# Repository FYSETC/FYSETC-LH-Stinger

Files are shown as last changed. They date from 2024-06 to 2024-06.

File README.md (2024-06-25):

# FYSETC-LH-Stinger
FYSETC LH-Stinger 3D printer library

# Introduction

This is a project from lhndo community,LH-Stinger . We made a little upgrade and improvement on the basis of this project, and provided a complete set of information. Thanks to the open source materials and support provided by Andrei, and hope you like it. You can find LH-Stinger official information below.

1.LH-Stinger Official website：

https://github.com/lhndo/LH-Stinger

2.LH-Stinger FYSETC Kit Wiki：
https://github.com/lhndo/LH-Stinger/wiki/FYSETC-Kit#issues

# BOM

[ LH-Stinger](https://github.com/FYSETC/FYSETC-LH-Stinger/blob/main/BOM.md)

# STL changes

### FYSETC LH-Stinger STLs changes
The following parts are required to match the component configuration of the FYSETC kit:

Toolhead:
[Toolhead Dragon UHF + Sherpa Mini](https://github.com/lhndo/LH-Stinger/tree/main/User_Mods/Toolhead/Toolhead%20Dragon%20UHF%20%2B%20Sherpa%20%20Mini%20-%20%40LH)

Aux Fan:
[Flap UHF x2](https://github.com/lhndo/LH-Stinger/blob/main/STL/Printer/Aux%20Fan/Flap%20UHF%20x2.stl)
Included in [STL/Aux Fan Parts.3mf ](https://github.com/lhndo/LH-Stinger/tree/main/STL)(Plate: Optional UHF )

Ebox:
[FYSETC Spider Mount](https://github.com/lhndo/LH-Stinger/tree/main/User_Mods/Ebox/FYSETC%20Spider%20V3%20Mount%20-%20%40MakerMylo)
Panel Bottom for LM200-22B48R2 Power Supply Check it [here](https://github.com/FYSETC/FYSETC-LH-Stinger/tree/main/STLs/Panel%20Bottom%20for%20LM200-22B48R2%20Power%20Supply)

LHS Breakbeat - Breakout Box:
[Breakout Box](https://github.com/lhndo/LH-Stinger/tree/main/STL/Printer/Breakout%20Box)
Included in [STL/Breakout Box Parts.3mf](https://github.com/lhndo/LH-Stinger/tree/main/STL)

# Wiring

### FYSETC LH-Stinger kit wiring



# Installation Guide

LH-Stinger Assembly manual [here](https://github.com/lhndo/LH-Stinger/wiki/Assembly-Guide).

MakerMylo Assembly manual [here](https://help.mylo.fun/makermylo-documents/fysetc/lh-stinger/youtube-build-series).

# Firmware&OS

Check it [here](https://github.com/FYSETC/FYSETC-LH-Stinger/tree/main/Klipper_Config).

# Videos

### Original LH-Stinger Videos [here](https://www.youtube.com/channel/UCPD2Ai4b49gVoCFSGFWoSdw).

# Support

FYSETC Facebook group: 

https://www.facebook.com/groups/238970713918171

FYSETC Discord:

https://discord.gg/T3XcJPgr

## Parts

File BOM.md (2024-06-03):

# Package list 

## LH Stinger Revision 1.0

| Index | Sort | Component | Qty | Note |
| ----- | --- | --- | --- | --- |
| 1 | Fasteners | LH Stinger fasteners Pack（12.9） | 1 SET  | |
| 2 | Frame | X Gantry 2020 323mm | 1 PC | |
| 3 | Frame | Y 3090 345mm | 1 PC | |
| 4 | Frame | Z Pillars 3060 400mm | 2 PCS  | |
| 5 | Frame | Z Top 3030 400mm | 1 PC | |
| 6 | Frame | Z Bottom 3090 400mm | 1 PC | |
| 7 | Frame | Y Rubber Feet 28 x 22 x 16.5mm | 4 PCS  | |
| 8 | Frame | Z Frame Feet - Flat Rubber, Neoprene Stiff Foam - 5mm, 1/4"  | 2 PCS  | |
| 9 | Frame | T Bracket Plate (Bottom,Enlarging the hole) | 2 PCS  | |
| 10 | Frame | Three Way Corner | 2 PCS  | |
| 11 | Frame | Bracket 90 No Tabs | 4 PCS  | |
| 12 | Frame | Bracket 90 No Tabs (Enlarging the hole) | 2 PCS  | |
| 13 | Frame | Bracket 90 Cast Tabs | 4 PCS  | |
| 14 | Motion | MGN 12H 300mm (Z1+ preload) stainless steel  440C | 3 PCS  | |
| 15 | Motion | MGN 12H 250mm (Z1+ preload) stainless steel  440C | 2 PCS  | |
| 16 | Motion | GATES GT2 Belt Loop (6mm W) - 188mm | 2 PCS  | |
| 17 | Motion | GATES GT2 Open Belt LL-2GT-6 (6mm wide) - 3000mm | 1 PC | |
| 18 | Motion | GATES GT2 Open Belt LL-2GT-9 (9mm wide) - 1000mm | 1 PC | |
| 19 | Motion | Pulley Gates 2GT 6mm Runice | 5 PCS  | |
| 20 | Motion | Pulley Gates 2GT 9mm (max 20mm height) Runice | 2 PCS  | |
| 21 | Motion | Pulley Gates 2GT 80 Tooth 6mm Runice | 2 PCS  | |
| 22 | Motion | Idler Gates 2GT 6mm Tooth (15mm outer ring diameter) Runice  | 3 PCS  | |
| 23 | Motion | Idler Gates 2GT 9mm Tooth Runice | 2 PCS  | |
| 24 | Motion | Bearing 625 2RS FUSHI | 8 PCS  | |
| 25 | Motion | Shaft Round 5x25mm (Idlers) | 3 PCS  | |
| 26 | Motion | Shaft Round 5x30mm (Idlers) | 2PCS | |
| 27 | Motion | D shaft 50x5mm (Z stack) | 1 PC | |
| 28 | Motion | D shaft 72x5mm (Z stack) | 1 PC | |
| 29 | Buildplate  | LH Stinger 200 CF Bed set | 1 SET  | |
| 30 | Buildplate  | PEI Film (200 mm^2) | 1 PC | |
| 31 | Buildplate  | Hotbed Kit for 200x200 220W | 1 PC | |
| 32 | Buildplate  | PI tape (50mm Width ，30M length) | 1 PC | |
| 33 | Misc | Sherpa mini CNC Extruder | 1 SET  | |
| 34 | Misc | Dragon Hotend UHF | 1 SET  | |
| 35 | Misc | Heater Cartridge 24V 70W | 1 PC | |
| 36 | Misc | Thermistor PT1000 | 1 PC | |
| 37 | Controller  | Spider H723 Board | 1 SET  | |
| 38 | Electronics | Raspberrypi 4b 2GB | 1 SET  | Optional |
| 39 | Electronics | MicroSD Card 16 GB | 1 PC | |
| 40 | Electronics | USB A to USB C - 25cm | 1PC | |
| 41 | Electronics | TMC2209 Stepper Motor Driver | 3 PCS  | |
| 42 | Electronics | TMC5160 Stepper Motor Driver | 3 PCS  | |
| 43 | Electronics | Nozzle Input Shaper | 1 PC | |
| 44 | Electronics | NEMA17 Stepper motors 42HS3418-22B19  (check [here](https://github.com/FYSETC/FYSETC-LH-Stinger/tree/main/Stepper%20motor%20parameters) | 2 PCS  | |
| 45 | Electronics | NEMA17 Stepper motors 42HSC6406C-24B20  (check [here](https://github.com/FYSETC/FYSETC-LH-Stinger/tree/main/Stepper%20motor%20parameters)） | 3 PCS  | |
| 46 | Electronics | Power Supply  Meanwell LSR-350 | 1 PC | |
| 47 | Electronics | Power Supply MORNSUN LM200-22B48R2 (HV X, Y Steppers) | 1 PC | |
| 48 | Electronics | Raspberry Pi communication cable | 1 PC | |
| 49 | Electronics | Dual Ball FAN - 5015 24V (Part Fan) | 2 PCS  | |
| 50 | Electronics | Dual Ball FAN - 4010 24V(Hotend Fan) | 1 PC | |
| 51 | Electronics | Dual Ball FAN - 6025 24V (Ebox Fan) | 2 PCS  | |
| 52 | Electronics | Dual Ball FAN - 9733 24V (AUX Fan) | 2 PCS  | |
| 53 | Electronics | Microswitch OMRON D2F-5 (Quickdraw Probe) with wire | 1 PC | |
| 54 | Electronics | 3 PIN Omron Endstops with wire | 3 PCS  | |
| 55 | Electronics | AC 250V 3 Terminal Power Socket with Fuse | 1 SET  | |
| 56 | Electronics | AC Power Cord | 1 PC | |
| 57 | Misc | Wiring kit（Pre-crimped terminals and longer wire lengths with label） | 1 SET  | |
| 58 | Electronics | LHS Breakbeat Board | 1 SET  | |
| 59 | Misc | Weaving casing 5mm 2.5M | 1 PC | |
| 60 | Misc | Weaving casing 8mm 2.0M | 1 SPC  | |
| 61 | Misc | Tension spring | 8 PCS  | |
| 62 | Misc | 4mm Bowden Coupler | 2 PCS  | |
| 63 | Misc | PTFE Tube (4mm OD 2mm ID) - 0.1m | 1 PC | |
| 64 | Misc | PTFE Tube (4mm OD 3mm ID) - 0.6m | 1 PC | |
| 65 | Misc | 6x3 Round Magnet (Quickdraw and Y Belt Set Tool) | 12 PCS | |
| 66 | Misc | Cutting pliers | 1 PC | |
| 67 | Misc | Hexagonal wrenchs | 1 SET  | |
| 68 | Misc | Thermal silica | 1 PC | |
| 69 | Misc | Ties | 20 PCS | |

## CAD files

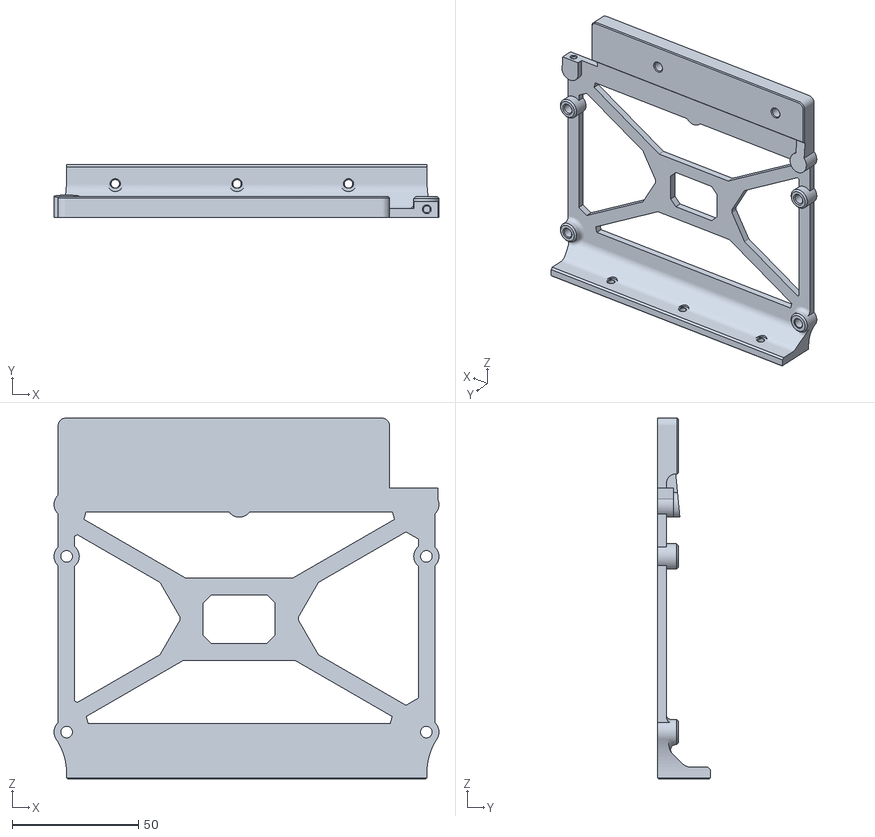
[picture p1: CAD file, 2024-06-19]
STLs/Mount Spider H7/Mount Spider H7.STL
152.3 x 20.8 x 142.7

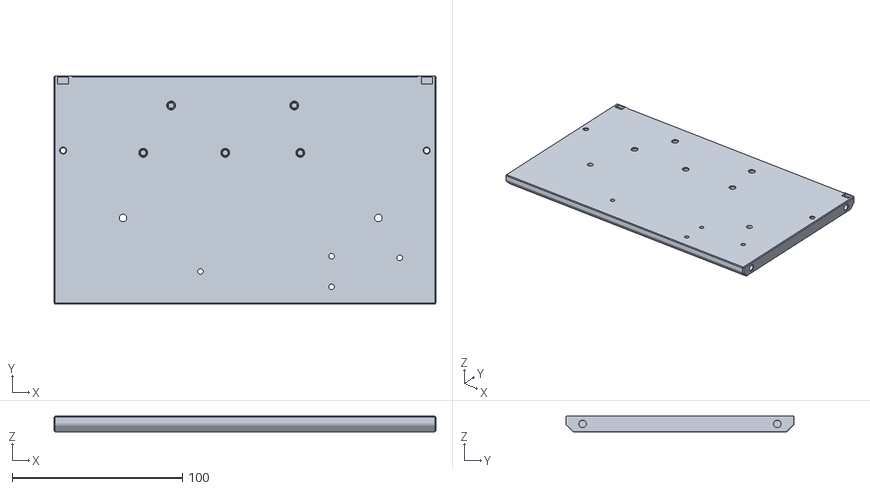
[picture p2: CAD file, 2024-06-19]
STLs/Panel Bottom for LM200-22B48R2 Power Supply/Panel Bottom.STL
224.4 x 134.2 x 9.37

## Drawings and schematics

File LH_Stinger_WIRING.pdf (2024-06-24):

# Spider v3.0 H7 LH Stinger V1.0

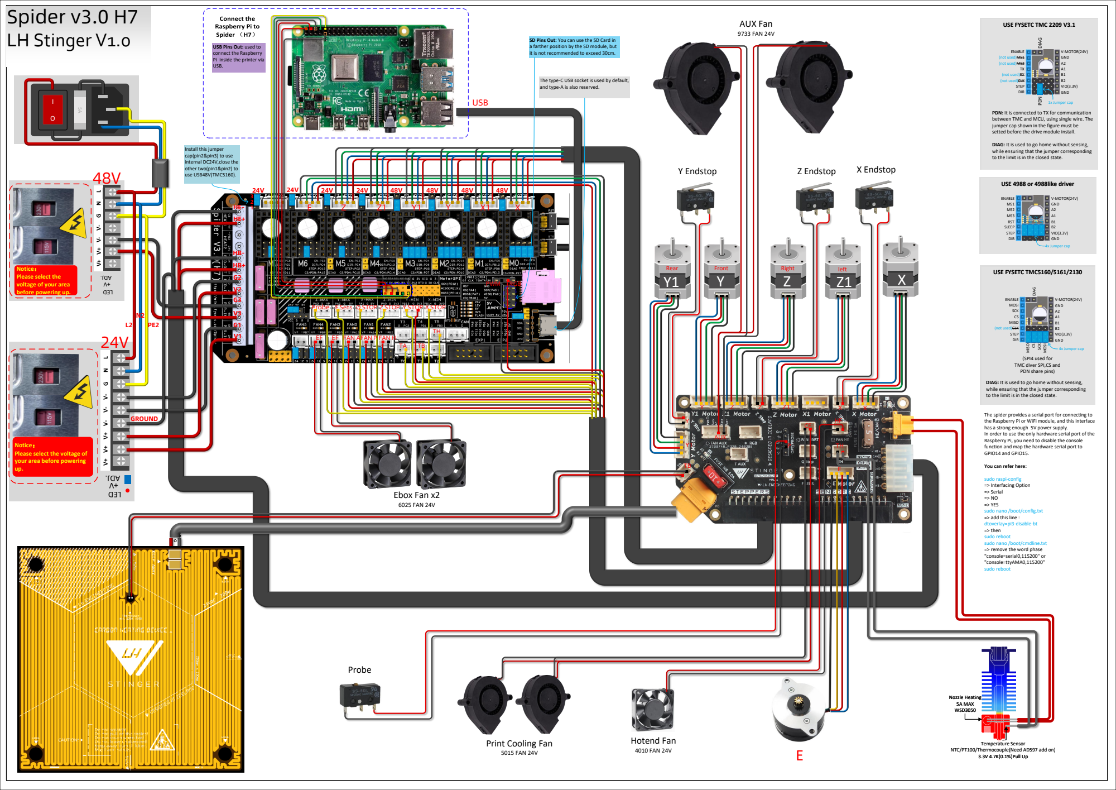
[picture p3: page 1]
USE FYSETC TMC5160/5161/2130; MOSI; SCK; MISO; V-MOTOR(24V) GND A2 A1 B1 B2 VIO(3.3V) GND; ENABLE (not used)MS1 (not used)MS2 TX; STEP DIR; PDN DIAG; 1x Jumper cap; 4x Jumper cap; ENABLE MOSI SCK CS MISO; DIAG; ENABLE MS1 MS2 MS3 RST SLEEP STEP DIR; SLEEP; Nozzle Heating 5A MAX WSD3050; Temperature Sensor; 3.3V 4.7K(0.1%)Pull Up; Hotend Fan; 4010 FAN 24V; Ebox Fan x2; 6025 FAN 24V; AUX Fan; 9733 FAN 24V; USB; PWM; RGB; Y Endstop; Z Endstop; X Endstop; Probe; AUX; Rear; Front; Right; left; GROUND

USE FYSETC TMC 2209 V3.1

SD Pins Out: You can use the SD Card in
a farther position by the SD module, but
it is not recommended to exceed 30cm.

USB Pins Out: used to
connect the Raspberry
Pi inside the printer via
USB.

(not used)RX
(not used)CLK

The type-C USB socket is used by default,
and type-A is also reserved.

PDN: It is connected to TX for communication
between TMC and MCU, using single wire. The
jumper cap shown in the figure must be
setted before the drive module install.

DIAG: It is used to go home without sensing,
while ensuring that the jumper corresponding
to the limit is in the closed state.

Install this jumper
cap(pin2&pin3) to use
internal DC24V,close the
other two(pin1&pin2) to
use USB48V(TMC5160).

USE 4988 or 4988like driver

Notice：
Please select the
voltage of your area
before powering up.

Probe F Sens Q STOP Z STOP Y STOP X STOP

FAN AFAN P FAN H

(SPI4 used for
TMC diver SPI,CS and
PDN share pins)

The spider provides a serial port for connecting to
the Raspberry Pi or WiFi module, and this interface
has a strong enough 5V power supply.
In order to use the only hardware serial port of the
Raspberry Pi, you need to disable the console
function and map the hardware serial port to
GPIO14 and GPIO15.

Please select the voltage of
your area before powering

You can refer here:

sudo raspi-config
=> Interfacing Option
=> Serial
=> YES
sudo nano /boot/config.txt
=> add this line :
dtoverlay=pi3-disable-bt
=> then
sudo reboot
sudo nano /boot/cmdline.txt
=> remove the word phase
"console=serial0,115200" or
"console=ttyAMA0,115200"

Print Cooling Fan
5015 FAN 24V

NTC/PT100/Thermocouple(Need AD597 add on)

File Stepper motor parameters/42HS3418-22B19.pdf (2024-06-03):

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

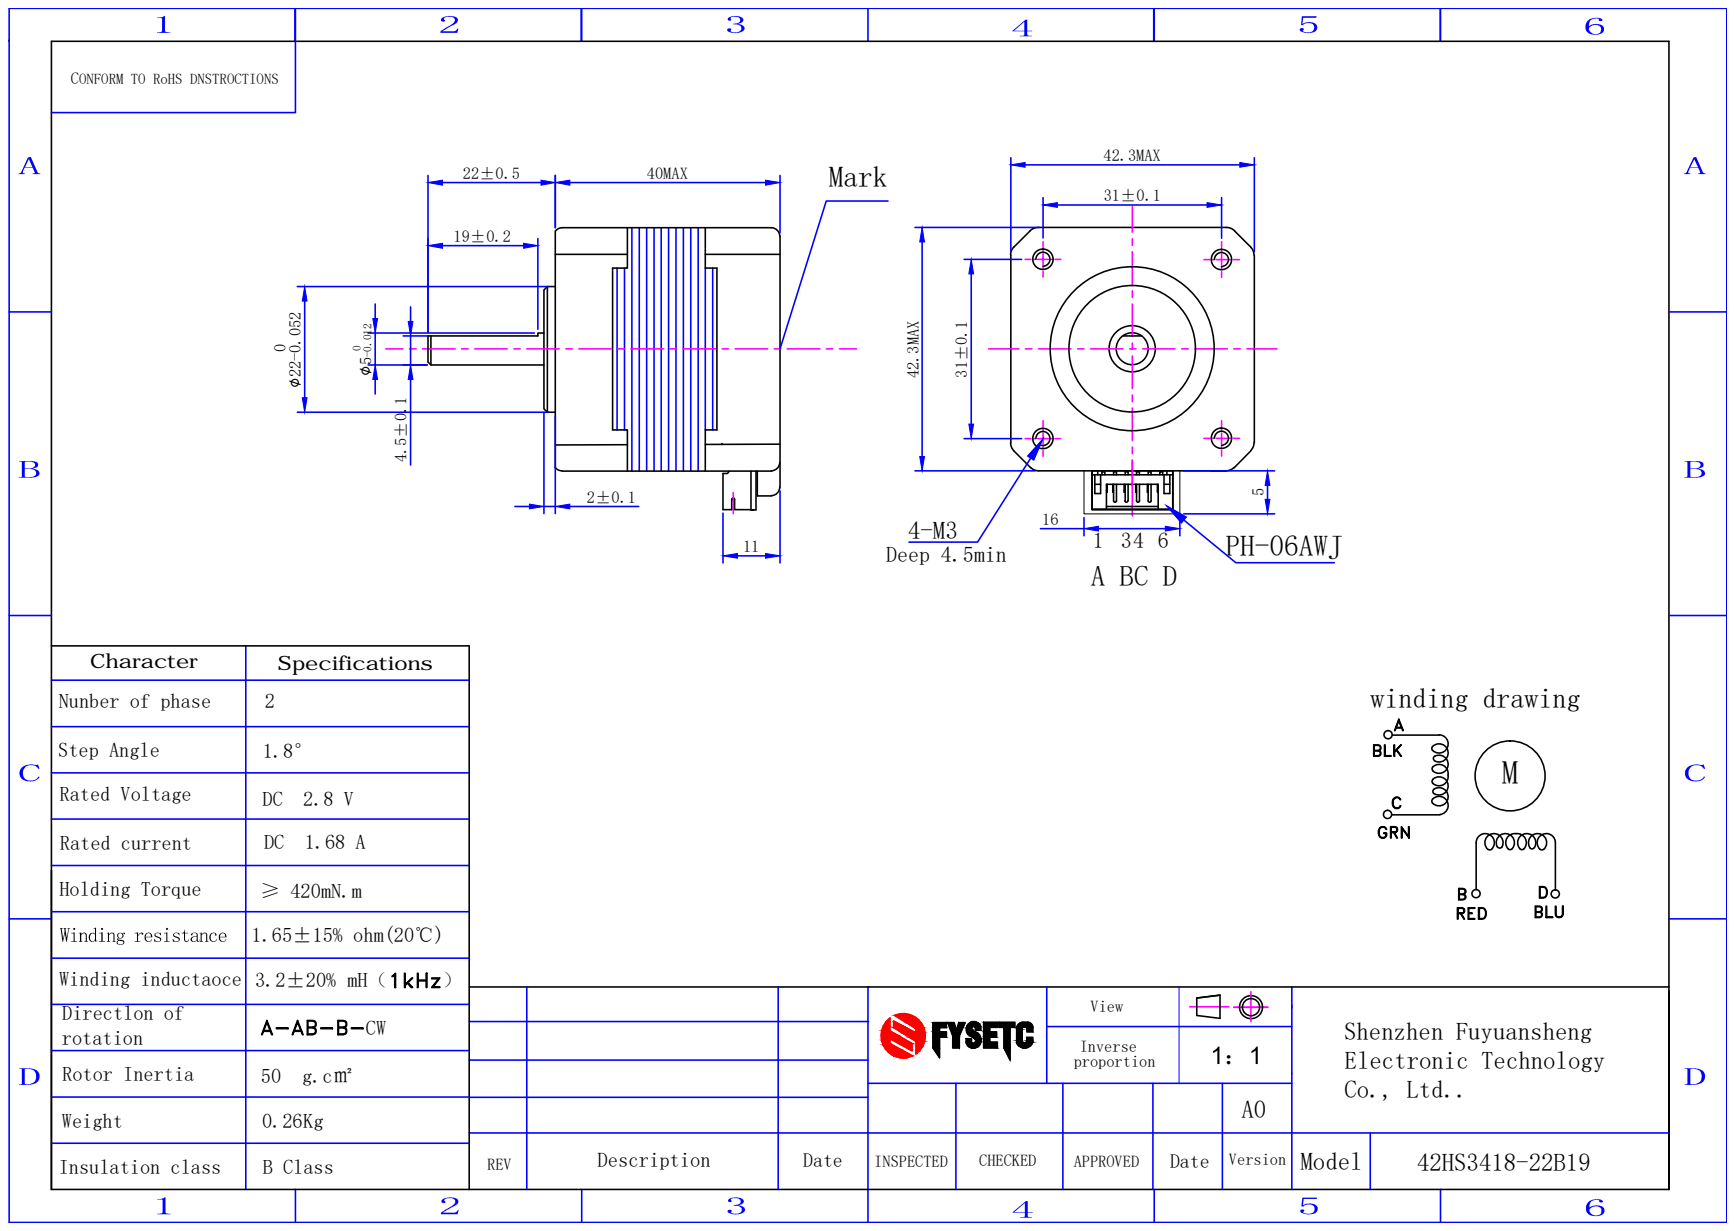
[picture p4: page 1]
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

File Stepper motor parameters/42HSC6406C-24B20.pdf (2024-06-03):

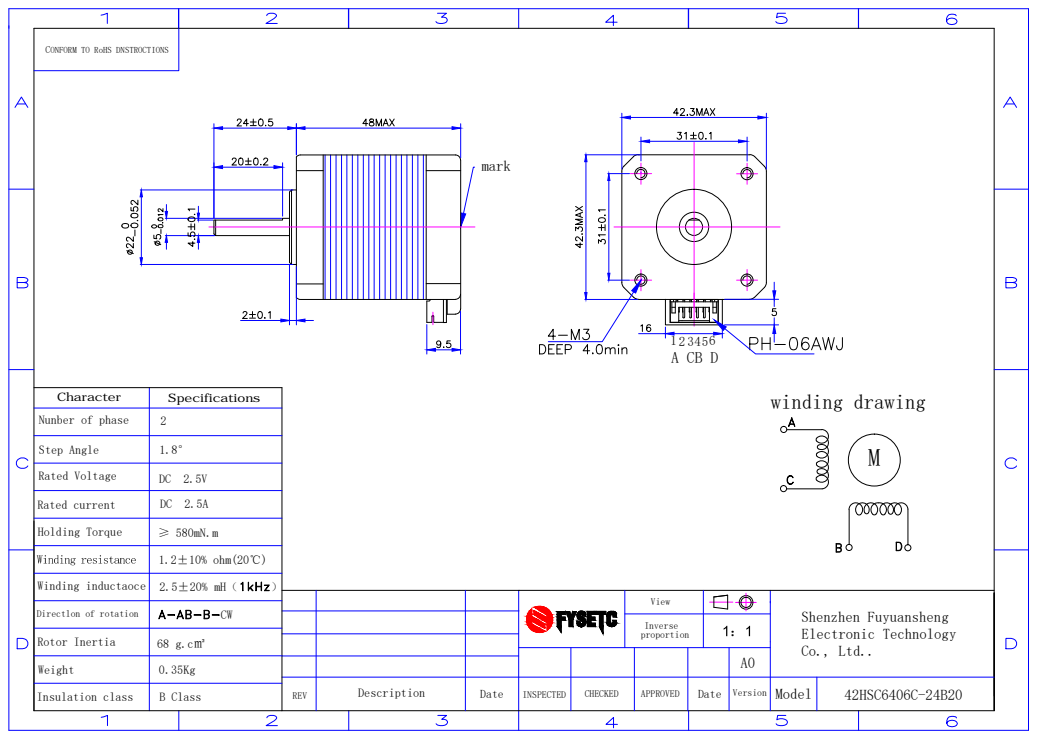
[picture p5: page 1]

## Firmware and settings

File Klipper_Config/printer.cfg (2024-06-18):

###############  LH STINGER  ##################
###________________________________________________
#    __          __  __________    __  ___   __  __  
#   / /  /\  /\ / _\/__   \_   \/\ \ \/ _ \ /__\/__\ 
#  / /  / /_/ / \ \   / /\// /\/  \/ / /_\//_\ / \// 
# / /__/ __  /  _\ \ / //\/ /_/ /\  / /_\\//__/ _  \ 
# \____|/ /_/   \__/ \/ \____/\_\ \/\____/\__/\/ \_/    
###________________________________________________
### Fysetc Spider 3.0 - STM32H723VGT6
###
### Flash with (H723 ver. only):
### "128KiB bootloader" and a "25Mhz crystal"
### USB Communication interface (PA11/PA12)
###
### For Other Octopus Pro chips, please consult: 
###https://github.com/FYSETC/FYSETC-SPIDER/tree/main/firmware/Klipper
###_______________________________________________

# Complete your configuration setup and check by following this guide: https://www.klipper3d.org/Config_checks.html

[include mainsail.cfg] # Mainsail or Fluid configuration choice, depending on your Klipper installation
# [include fluidd.cfg]

[include std_kinematics.cfg]  # Decoupled Kinematic settings. In case of running Limited Cartesian Kinematics:  https://klipper.discourse.group/t/independant-acceleration-limits-for-x-and-y-axes/3831

[include steppers.cfg] # Daily print stepper driver configuration. Choose one or the other.

# [include steppersfast.cfg]  # High performance stepper driver configuration. Choose one or the other.

[include quickdrawprobe.cfg] # Install the Quickdraw Probe Extension by Daalegard. For instructions please see quickdrawprobe.cfg 

# [include adxl_pico.cfg] # Enable when connecting the Rpi Pico + ADXL 

[include reshelper.cfg] # Install Reshelper from: https://github.com/lhndo/ResHelper

[include mymacros.cfg]  # Your Macros

[include testspeed.cfg] # Speed Testing Macros 

[include KAMP_Settings.cfg]    # Install KAMP from: https://github.com/kyleisah/Klipper-Adaptive-Meshing-Purging

###__________________  MCU  ____________________

[mcu]
serial: /dev/serial/by-id/usb-Klipper_stm32h723xx_280005001451323032333536-if00
# To find your USB serial addres run: ls /dev/serial/by-id/*

###_______________  Steppers  ___________________

[stepper_x]  ;  M0
step_pin: PE11
dir_pin: !PE10
enable_pin: !PE9
endstop_pin: ^PB14
full_steps_per_rotation: 200
rotation_distance: 40
position_endstop: 0
position_min: 0
position_max: 254
homing_speed: 80
homing_retract_dist: 0

#[stepper_x1]   ;  M1
#step_pin: PD8
#dir_pin: !PB12
#enable_pin: !PD9
#endstop_pin: ^PB13
#full_steps_per_rotation: 200
#rotation_distance: 40
#position_endstop: 0
#position_min: 0
#position_max: 255
#homing_speed: 80
#homing_retract_dist: 0

[stepper_y]   ;  M2
step_pin: PD14
dir_pin: !PD13
enable_pin: !PD15
endstop_pin: ^PB13
full_steps_per_rotation: 200
rotation_distance: 40
position_endstop: 0
position_min: 0
position_max: 255
homing_speed: 80
homing_retract_dist: 0

[stepper_y1]   ;  M3
step_pin: PD5
dir_pin: PD6
enable_pin: !PD4
endstop_pin: ^PB13
full_steps_per_rotation: 200
rotation_distance: 40

[stepper_z]   ;  M4
step_pin: PE2
dir_pin: PE4
enable_pin: !PE3
#endstop_pin: ^PA0    # Disable when activating quickdrawprobe.cfg
endstop_pin: probe:z_virtual_endstop     # Enable when activating quickdrawprobe.cfg
full_steps_per_rotation: 200
rotation_distance: 40
gear_ratio: 80:20
#position_endstop: 0    # Disable when activating quickdrawprobe.cfg
position_min: -35
position_max: 196
homing_speed: 10
second_homing_speed: 4
homing_retract_dist:3

[stepper_z1]  ;  M5
step_pin: PE6
dir_pin: !PC13
enable_pin: !PE5
# endstop_pin: PA0    # Disable when activating quickdrawprobe.cfg
full_steps_per_rotation: 200
rotation_distance: 40
gear_ratio: 80:20

[probe]  # Enable when activating quickdrawprobe.cfg
#z_offset: 9 # calibrate with PROBE_CALIBRATE command. After calibrating and saving this like will be automatically commented. 

###_______________  Extruder/Bed  ___________________

[extruder]   ;  M6
step_pin: PD12
dir_pin: PC4
enable_pin: !PE8
heater_pin: PC8   # Disable when the hotend thermistor is connected though MAX31865 
sensor_pin: PB0 #PC2  #T2
sensor_type: PT1000 #Generic 3950

# ____ MAX31865 Configuration ____
#heater_pin: PA0 # HE0
#sensor_type: MAX31865
#spi_bus: spi1
#sensor_pin: PF8
#rtd_nominal_r: 1000
#rtd_num_of_wires: 2
#rtd_reference_r: 4300
#rtd_use_50Hz_filter: True
#_________________________________

rotation_distance: 3.584
full_steps_per_rotation: 200
smooth_time: 3
min_temp: -270
max_temp: 310
min_extrude_temp: 170
nozzle_diameter: 0.400
filament_diameter: 1.750
max_extrude_only_distance: 1000.0
max_extrude_only_velocity: 120
max_extrude_cross_section: 5
pressure_advance: 0.02
pressure_advance_smooth_time: 0.02
instantaneous_corner_velocity: 1.000
control: pid
pid_Kp: 15.547 
pid_Ki: 0.596 
pid_Kd: 101.447

[heater_bed]
heater_pin: PB4
sensor_pin: PC1 # T1
sensor_type: Generic 3950
smooth_time: 1
min_temp: 0
max_temp: 110
control: pid
pid_Kp: 48.004 
pid_Ki: 0.446 
pid_Kd: 1292.517

###_______________  Fans  ___________________

#  Fan 0 - Optional Auxiliary Fan
[fan_generic aux]
pin: PA13
kick_start_time: 0.500

# Fan 1 - Part Cooling Fan
[fan]
#pin: multi_pin:Print_Fan
pin: PA14
cycle_time: 0.024
kick_start_time: 0.5
hardware_pwm: False
max_power: 1.0

# Fan 2 - Hotend Cooling Fan
[heater_fan hotend_fan]  
pin: PB2
heater: extruder
heater_temp: 50.0
kick_start_time: 0.500
hardware_pwm: False
cycle_time: 0.024
fan_speed: 0.72

# Fan3 & Fan4
[temperature_fan ebox_stm32] 
pin: multi_pin:ebox_Fan
kick_start_time: 0.2
sensor_type:temperature_mcu
off_below: 0.2
max_power: 1.0
control:watermark
min_temp: 10
max_temp: 100
target_temp: 20.0

# ebox_Fan
[multi_pin ebox_Fan]
pins: PB6,PB5

###_______________  Temperature Sensors  ___________________
# T1
#[temperature_sensor external]
#sensor_pin:PC1
#sensor_type: ATC Semitec 104GT-2
#min_temp: 0
#max_temp: 300

[temperature_sensor Pi]
sensor_type: temperature_host
min_temp: 0
max_temp: 100

###_______________  Features  ___________________

[idle_timeout]
timeout: 600
gcode:
  {% if printer.pause_resume.is_paused %}
    M118 Idle timeout while paused, turning off hotend
    SET_HEATER_TEMPERATURE HEATER=extruder TARGET=0
  {% else %}
    M118 Idle timeout, turning off hotend and disabling steppers
    TURN_OFF_HEATERS
    M84
  {% endif %}

[exclude_object]
[respond]
[resonance_holder]
accel_per_hz: 140
[display_status]
[force_move]
enable_force_move: true
[respond]
default_type: echo
default_prefix:
[gcode_arcs]
resolution: 0.1


[display]
lcd_type:ssd1306
#   Set to either "ssd1306" or "sh1106" for the given display type.
#i2c_mcu:
#i2c_bus:
#i2c_software_scl_pin:
#i2c_software_sda_pin:
#i2c_speed:
#   Optional parameters available for displays connected via an i2c
#   bus. See the "common I2C settings" section for a description of
#   the above parameters.
cs_pin:PD2
dc_pin:PC12
#spi_speed:
#spi_bus:
spi_software_sclk_pin:PC11
spi_software_mosi_pin:PC10
spi_software_miso_pin:PA7
#   The pins connected to the lcd when in "4-wire" spi mode. See the
#   "common SPI settings" section for a description of the parameters
#   that start with "spi_". The default is to use i2c mode for the
#   display.
reset_pin:PC7
#   A reset pin may be specified on the display. If it is not
#   specified then the hardware must have a pull-up on the
#   corresponding lcd line.
contrast:239
#   The contrast to set. The value may range from 0 to 256 and the
#   default is 239.
vcomh: 31
#   Set the Vcomh value on the display. This value is associated with
#   a "smearing" effect on some OLED displays. The value may range
#   from 0 to 63. Default is 0.
invert: False
#   TRUE inverts the pixels on certain OLED displays.  The default is
#   False.
# x_offset: 2
#   Set the horizontal offset value on SH1106 displays. The default is
#   0.


#*# <---------------------- SAVE_CONFIG ---------------------->
#*# DO NOT EDIT THIS BLOCK OR BELOW. The contents are auto-generated.
#*#
#*# [probe]
#*# z_offset = 8.800
#*#
#*# [bed_mesh default]
#*# version = 1
#*# points =
#*# 	  0.043784, -0.040200, -0.040591
#*# 	  0.007847, -0.002114, 0.005503
#*# 	  0.009214, 0.018589, 0.051987
#*# x_count = 3
#*# y_count = 3
#*# mesh_x_pps = 2
#*# mesh_y_pps = 2
#*# algo = lagrange
#*# tension = 0.2
#*# min_x = 82.69
#*# max_x = 157.65
#*# min_y = 100.98
#*# max_y = 175.36

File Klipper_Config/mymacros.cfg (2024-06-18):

##### Variables #####

[gcode_macro _CLIENT_VARIABLE]
variable_use_custom_pos  : True ; use custom park coordinates for x,y [True/False] 
variable_custom_park_x   : 10.0   ; custom x position; value must be within your defined min and max of X
variable_custom_park_y   : 200.0   ; custom y position; value must be within your defined min and max of Y
variable_custom_park_dz  : 80.0   ; custom dz value; the value in mm to lift the nozzle when move to park position 
variable_retract         : 1.0   ; the value to retract while PAUSE
variable_cancel_retract  : 3.0   ; the value to retract while CANCEL_PRINT
variable_speed_retract   : 35.0  ; retract speed in mm/s
variable_unretract       : 1.0   ; the value to unretract while RESUME
variable_speed_unretract : 35.0  ; unretract speed in mm/s
variable_speed_hop       : 15.0  ; z move speed in mm/s
variable_speed_move      : 80.0 ; move speed in mm/s
variable_park_at_cancel  : True ; allow to move the toolhead to park while execute CANCEL_PRINT [True,False]
variable_park_at_cancel_x : 10  ; different park position during CANCEL_PRINT [None/Position as Float]; park_at_cancel must be True
variable_park_at_cancel_y : 200  ; different park position during CANCEL_PRINT [None/Position as Float]; park_at_cancel must be True
# !!! Caution [firmware_retraction] must be defined in the printer.cfg if you set use_fw_retract: True !!!
variable_use_fw_retract  : False ; use fw_retraction instead of the manual version [True/False] 
variable_idle_timeout     : 0     ; time in sec until idle_timeout kicks in. Value 0 means that no value will be set or restored


### Custom Variables ##
# Filament Load
variable_my_load_len : 65.0
variable_my_load_prime_len: 44.0
variable_my_unload_len: 50.0
variable_my_purge_len: 50.0

# Aux Fan
variable_has_aux_fan: False    ; Aux fan should be defined as [fan_generic aux] in printer.cfg
variable_is_aux_linked: True  ; Linking Aux fan speeds with Part fan
variable_aux_ratio: 1  ; Ratio between Part fan and Aux when linked. 0.75 equals 75% of the Part fan speed

# Quiet Mode (Qmode)  # To enable quiet mode, trigger the Qmode macro, or set QUIETMODE=1 in the slicer print start parameters
variable_q_fan_max: 34 ; 0-100 - fan speeds defined as percentages: 0-100
variable_q_fan_aux: 14 ; 0-100
variable_q_feedrate: 80 ; 0-100
variable_q_velocity: 200
variable_q_accel: 5000
variable_q_accel_decel: 2500
variable_q_scv: 5
variable_q_pa_mult: 1.0  

# Utility
variable_automeshed: False    ; Do not set this variable. It is used internally by other macros to track the autogenerated KAMP mesh.


gcode:


##### Macros #####

[virtual_sdcard]
path: ~/printer_data/gcodes
on_error_gcode: 
  RESPOND TYPE=command MSG='Vritual SD error triggered. Starting CANCEL_PRINT'
  CANCEL_PRINT
  OFF

[gcode_macro RESET]
description: RESTART
gcode:
  RESTART



##### Slicer Macros #####

[gcode_macro PRINT_START_MICRO]
gcode:        
    # Parameters
    {% set bedtemp = params.BED|int %}
    {% set hotendtemp = params.HOTEND|int %}
    {% set autopurge = params.AUTOPURGE| default(0) | int %}
    {% set automesh = params.AUTOMESH| default(0) | int %}
  
    SAVE_GCODE_STATE NAME=print_start
    SET_VELOCITY_LIMIT VELOCITY=300 ACCEL=10000 ; Lower velocity for setup moves
    G90 
    M83
    M190 S{bedtemp}  #Heat bed

    PROBE_LOCK
    G28 #home
    Z_TILT_ADJUST SAMPLES=1 ACCURACY=1
    Z_TILT_ADJUST SAMPLES=2
    G28 Z
    {% if automesh == 0 %}  #Selecting bed mesh based on temperature. You need to have default, 80, and 105 profiles created.
      {% if bedtemp > 95 %}
        BED_MESH_PROFILE LOAD=105
      {% elif bedtemp > 69 %}
        BED_MESH_PROFILE LOAD=80
      {% else %}
        BED_MESH_PROFILE LOAD=default
      {% endif %}
    {% else %}
      BED_MESH_CLEAR
      BED_MESH_CALIBRATE # KAMP
      SET_GCODE_VARIABLE MACRO=_CLIENT_VARIABLE VARIABLE=automeshed VALUE=True
    {% endif %}

    PROBE_UNLOCK
    PROBE_DETACH
    G1 X20 Y20 Z20 F3000  # Safe spot to heat up nozzle
    M109 S{hotendtemp} # Heat hotend

    {% if  == 0 %}
      G1 E12.5 F600 # Prime nozzle

    {% else %}
      LINE_PURGE # KAMP
    {% endif %}
    
    SET_VELOCITY_LIMIT VELOCITY={printer.configfile.settings.printer.max_velocity} ACCEL={printer.configfile.settings.printer.max_accel}  ; Restore velocity to default
    G92 E0 # Reset Extruder
    RESPOND TYPE=command MSG='Print Started'
    RESTORE_GCODE_STATE NAME=print_start
    G90


[gcode_macro PRINT_END]
gcode:
    G91 # Absolute pos
    M83 # Relative Extrude
    G92 E0 # Reset Extruder
    G1 E-0.2 F{60*60} # Retract End
    G1 X-15 Z2 E-0.8 F{60*600} # Retract End
    G1 E-5 F{10*60} # Retract Tip Form 
    G1 E2 F{80*60}
    G1 E-6 F{10*60}
      
    {% set client = printer['gcode_macro _CLIENT_VARIABLE'] %}
    TURN_OFF_HEATERS # Safety call in case Park Fails
    RESPOND TYPE=command MSG='Print Ended! Turning things off.'
    {% if client.automeshed == True %}  # Clear KAMMP Bed Mesh
      BED_MESH_CLEAR
      BED_MESH_PROFILE REMOVE=default
    {% endif %}

    G90 # Absolute pos
    _TOOLHEAD_PARK_PAUSE_CANCEL
    OFF
    M117 Done!


[gcode_macro OFF]
gcode:
    M84                                  # turn steppers off
    TURN_OFF_HEATERS                     # turn bed / hotend off
    M107                                 # turn fans off
    #SET_FAN_SPEED FAN=Exhaust SPEED=0   # turn exhaust fan off
    #SET_FAN_SPEED FAN=BedFans SPEED=0   # bed fan off
    #SET_PIN PIN=caselight VALUE=0       # turn case light off
    RESPOND TYPE=command MSG='All OFF'


[gcode_macro M109] # Wait Hotend Temp
rename_existing: M109.1
gcode:
    #Parameters
    {% set s = params.S|float %}
    
    M104 {% for p in params %}{'%s%s' % (p, params[p])}{% endfor %}  # Set hotend temp
    {% if s != 0 %}
        TEMPERATURE_WAIT SENSOR=extruder MINIMUM={s} MAXIMUM={s+1}   # Wait for hotend temp (within 1 degree)
    {% endif %}


[gcode_macro M190] # Wait Bed Temp
rename_existing: M190.1
gcode:
    #Parameters
    {% set s = params.S|float %}

    M140 {% for p in params %}{'%s%s' % (p, params[p])}{% endfor %}   # Set bed temp
    {% if s != 0 %}
        TEMPERATURE_WAIT SENSOR=heater_bed MINIMUM={s} MAXIMUM={s+1}  # Wait for bed temp (within 1 degree)
    {% endif %}



#### Quiet Modes #####

[gcode_macro Qmode]
variable_flag: 0
variable_accel: 0
variable_accel_to_decel: 0
variable_velocity: 0
variable_square_corner_velocity: 0
variable_pressure_advance:0.0
variable_fan_value: 0.00
variable_fan_aux_value: 0.00
variable_fan2_value: 0.00
variable_speed_factor: 0
gcode:
  {% set printer_state = printer.print_stats.state %}
  {% set client = printer['gcode_macro _CLIENT_VARIABLE'] %}
  {% if printer['gcode_macro Qmode'].flag|int == 0 %}
      SET_GCODE_VARIABLE MACRO=Qmode VARIABLE=accel VALUE={printer.toolhead.max_accel}
      #SET_GCODE_VARIABLE MACRO=Qmode VARIABLE=accel_to_decel VALUE={printer.toolhead.max_accel_to_decel}
      SET_GCODE_VARIABLE MACRO=Qmode VARIABLE=velocity VALUE={printer.toolhead.max_velocity}
      SET_GCODE_VARIABLE MACRO=Qmode VARIABLE=square_corner_velocity VALUE={printer.toolhead.square_corner_velocity}
      SET_GCODE_VARIABLE MACRO=Qmode VARIABLE=pressure_advance VALUE={printer.extruder.pressure_advance}
      SET_GCODE_VARIABLE MACRO=Qmode VARIABLE=speed_factor VALUE={printer.gcode_move.speed_factor}
      SET_GCODE_VARIABLE MACRO=Qmode VARIABLE=fan_value VALUE={printer.fan.speed}
      {% if client.has_aux_fan == True %}
        SET_GCODE_VARIABLE MACRO=Qmode VARIABLE=fan_aux_value VALUE={printer['fan_generic aux'].speed}
      {% endif %}
      
 

      SET_TMC_FIELD STEPPER=stepper_x FIELD=TPWMTHRS value=0
      SET_TMC_FIELD STEPPER=stepper_y FIELD=TPWMTHRS value=0
      SET_TMC_FIELD STEPPER=stepper_y1 FIELD=TPWMTHRS value=0
      SET_TMC_FIELD STEPPER=stepper_z FIELD=TPWMTHRS value=0
      SET_TMC_FIELD STEPPER=stepper_z1 FIELD=TPWMTHRS value=0

      # Set Motion Parameters
      M220 S{client.q_feedrate} #set feedrate
      SET_VELOCITY_LIMIT VELOCITY={client.q_velocity}
      SET_VELOCITY_LIMIT ACCEL={client.q_accel}
      SET_VELOCITY_LIMIT ACCEL_TO_DECEL={client.q_accel_decel}
      SET_VELOCITY_LIMIT SQUARE_CORNER_VELOCITY={client.q_scv}
      SET_PRESSURE_ADVANCE ADVANCE={printer.extruder.pressure_advance*client.q_pa_mult}

     # Set Fan Parameters
     SET_GCODE_VARIABLE MACRO=M106 VARIABLE=max_fan VALUE={client.q_fan_max*2.54}
    
      {% if printer.fan.speed>(100/client.q_fan_max) %}
          M106 S{client.q_fan_max*2.54}
      {% endif %}
      {% if client.has_aux_fan == True and printer['fan_generic aux'].speed>100/client.q_fan_aux %}
         M106 P2 S{client.q_fan_aux*2.54}
      {% endif %}
      
      SET_GCODE_VARIABLE MACRO=Qmode VARIABLE=flag VALUE=1
      RESPOND TYPE=command MSG='Quiet Mode Active'
  {% endif %}
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

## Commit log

2024-06-03 Upload motor parameters
    Upload Stepper motor parameters
2024-06-03 Create BOM.md
    Upload BOM
2024-06-18 Upload the wiring diagram and config
    Upload the wiring diagram and config
    [Adaptive_Meshing.cfg, KAMP_Settings.cfg, Line_Purge.cfg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]
2024-06-19 Update STLs
    Update STLs
    [Mount Spider H7.STL, Panel Bottom.STL]
2024-06-21 Update wiring diagram
    Update wiring diagram
